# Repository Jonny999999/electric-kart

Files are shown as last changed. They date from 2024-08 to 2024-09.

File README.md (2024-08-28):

Firmware for Atmega-8 Microcontroller and kicad PCB-Files for a custom built electric kart.  
**Note:** The firmware and PCB files Version V1 were originally created in 2015, those have been added to this repository for archival purposes.

<br>

# Hardware Overview (vehicle)
- 2.9 kW Series wound motor (forklift)
- Custom pcb with Atmega-8 creating 124 Hz PWM
- Custom pcb with mosfet driver
- Custom pcb with relay on IGBT for emergency stop
- Audi gas pedal used as voltage divider 
- 600A IGBT (FUJI 1MBI600PX-140-01)
- Schottky diode

## Wiring plan
[doc/wiring-plan.drawio.pdf](doc/wiring-plan.drawio.pdf)
  
## Photos
<p align="center">
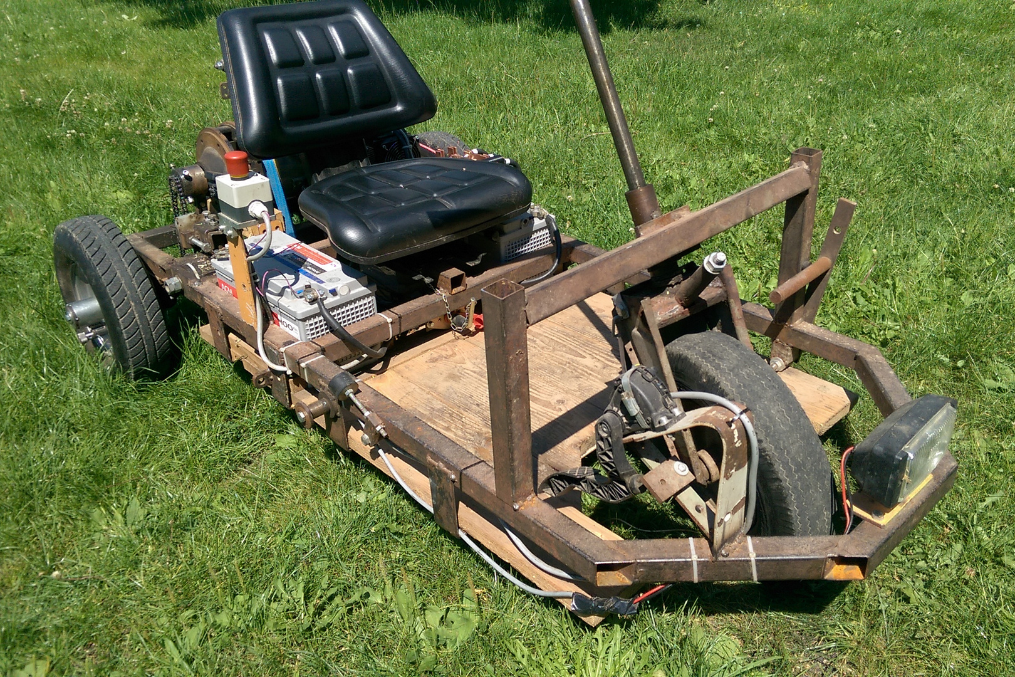
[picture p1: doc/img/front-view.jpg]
  
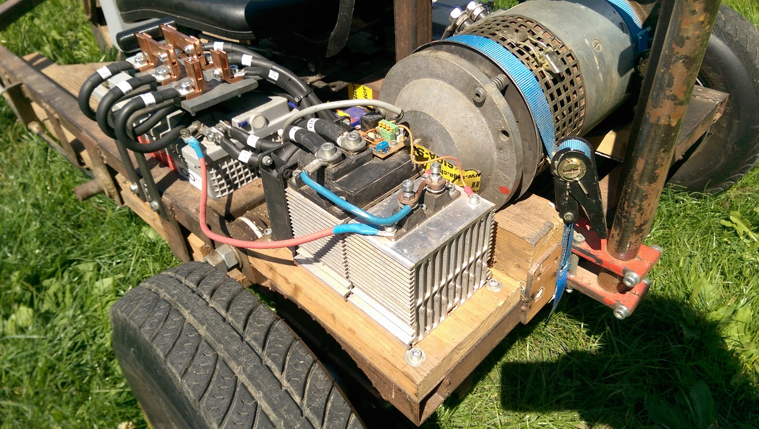
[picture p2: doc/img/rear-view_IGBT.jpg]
  
</p>

<br>

# Firmware
## Requirements
- avr-gcc
- avrdude
- make

## Compile
```bash
cd firmware/V1_fw-control-board
make
```

## Flash
Connect laptop to the board using an USB ISB-Programmer and run the commands:
```bash
make &&
sudo make upload
```
Note: `make upload` flashes the last compiled .elf file only  
-> also run `make` first for compiling and flashing the latest version.

## Current version
The current actually used project is located in [firmware/V2.1/](firmware/V2.1/).  
All other folders in [firmware/](firmware/) are for old board versions thus no longer used and archive only.

<br>

# Hardware (PCB Versions)
## V2.1
Rework of version V2.0 with more effort put into EMC to fix controller resets:
- 2 layer board
- 5V/GND for controller completely isolated from main batteries
  - isolated 5V DC-DC converter IC
  - more optocouplers: for driver, mosfet, relay and batt-voltage-threshold
- Strictly separate 5V and 24V components (separate GND planes, isolation gap)
- Front side is GND layer, Back side also has GND zones

Date: 2024.08.20  
Folder: [hardware/V2.1_board-ecar_isolated](hardware/V2.1_board-ecar_isolated/)  
Schematic: [hardware/V2.1_board-ecar_isolated/export/schematic.pdf](hardware/V2.1_board-ecar_isolated/export/schematic.pdf)
<br>
<br>
<p align="center">


</p>
<p align="center">

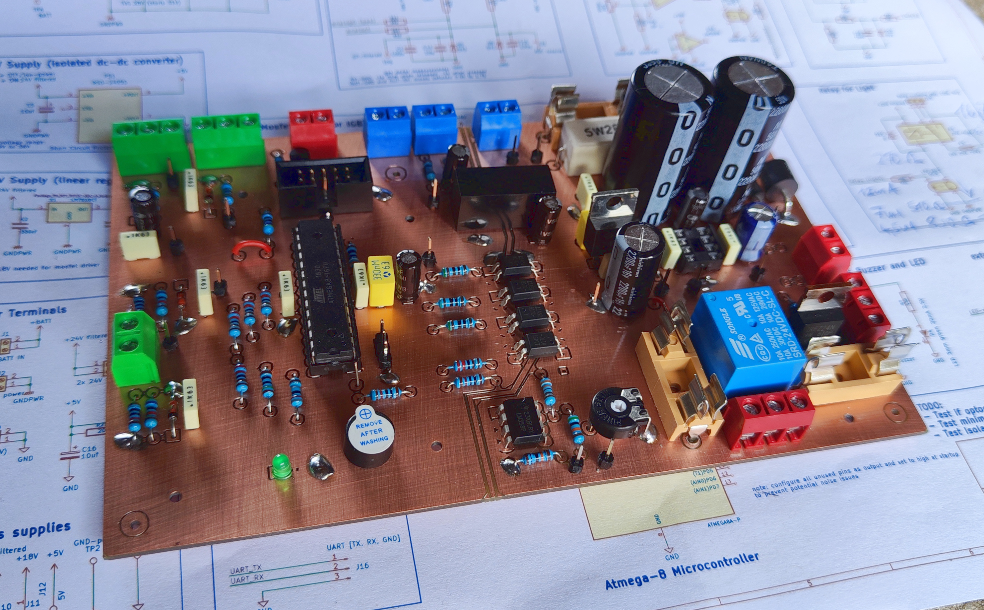
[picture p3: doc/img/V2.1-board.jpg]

</p>

## V2.0
V1.1 worked well for almost 9 years, the idea was to replace the corroded pcb and get rid of the separate supply batteries for the control board.  
Single board with controller, driver and newly added:
- supply filter
- buck converter
- relay  
  
Date: 2024.08.06  
Folder: [hardware/V2.0_board-ecar](hardware/V2.0_board-ecar)  
Schematic: [hardware/V2.0_board-ecar/export/schematic.pdf](hardware/V2.0_board-ecar/export/schematic.pdf)
<br>
<br>
<p align="center">

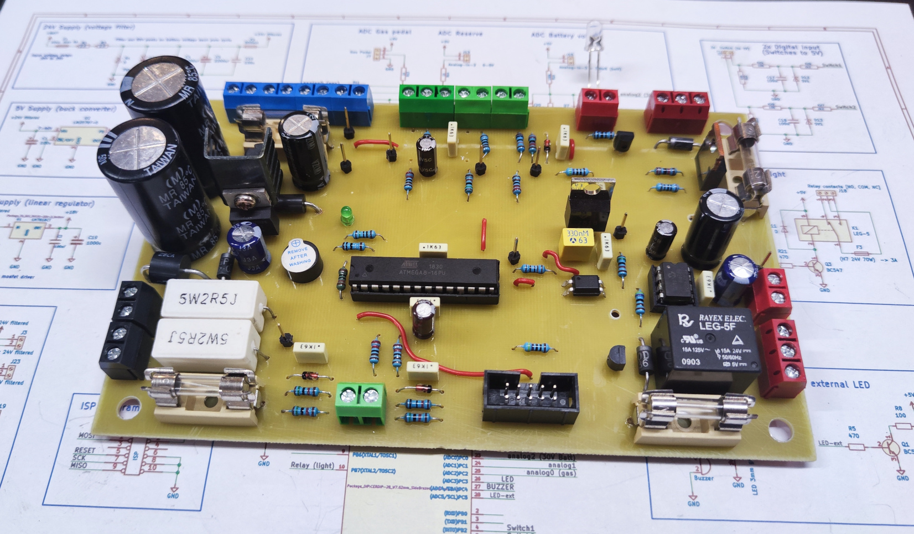
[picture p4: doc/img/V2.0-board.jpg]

</p>

**Fail:**  
Same problems as previous versions: When main batteries are used as supply for control pcb, the controller crashes at certain duty cycle.  
When Using an isolated supply (separate battery or lab supply) there is no issue. => peaks in supply voltage were not the issue and the filter did not really help, except preventing the voltage-regulators from burning out.  
<br>
**Issues:**  
- bad GND track (driver current shifts GND level for controller)
- bad routing overall (EMC)
- UART connector missing
- GND testpin missing

## V1.1
**separate driver board**  
Same control board from V1.0 but additional separate pcb with mosfet driver.  
Date: 2015.05.24  
Folder: [hardware/V1.1_driver-board-separate](hardware/V1.1_driver-board-separate)  
Schematic: [hardware/V1.1_driver-board-separate/export/schematic.pdf](hardware/V1.1_driver-board-separate/export/schematic.pdf)
<br>
<br>
<p align="center">
  
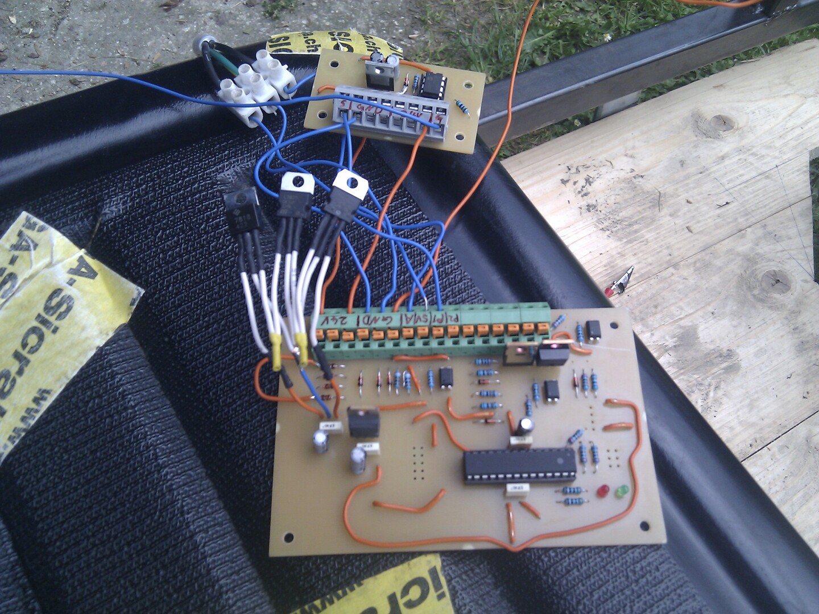
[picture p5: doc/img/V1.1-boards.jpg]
  
</p>

## V1.0
**control board**   
Date: 2015.05.14  
Folder: [hardware/V1.x_control-board](hardware/V1.x_control-board)  
Schematic: [hardware/V1.x_control-board/export/schematic.pdf](hardware/V1.x_control-board/export/schematic.pdf)
<br>
<br>


**Issues:**
- separate battery for control supply is necessary, when using main battery controller crashes when motor starts

**driver board on IGBT**  
pcb on IGBT with mosfet driver and relay (only the relay on this board is still used in V2.1)    
Folder: [hardware/V1.0_driver-board-on-igbt](hardware/V1.0_driver-board-on-igbt)  
Schematic: [hardware/V1.0_driver-board-on-igbt/export/schematic.pdf](hardware/V1.0_driver-board-on-igbt/export/schematic.pdf)
<br>
<br>
<p align="center">

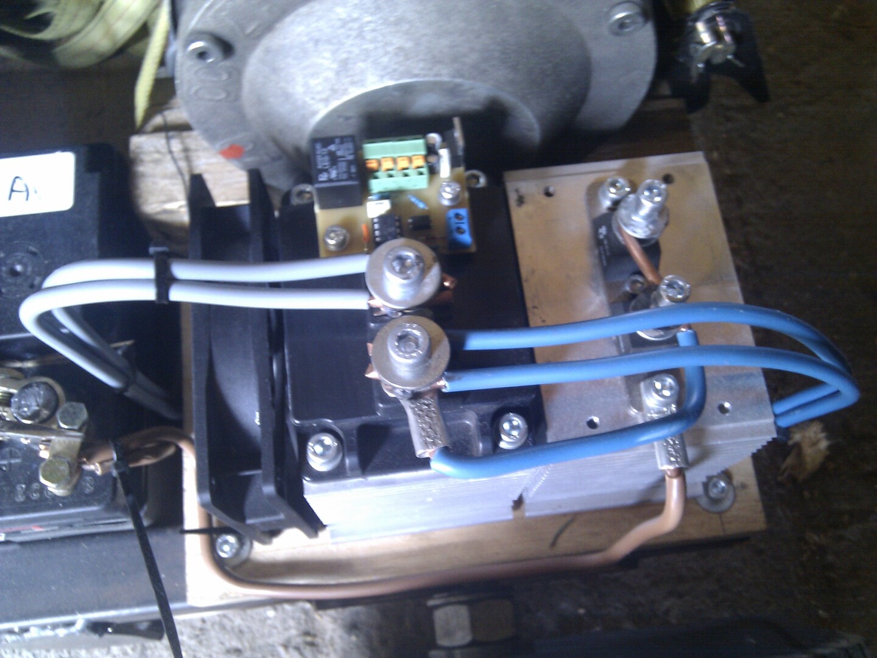
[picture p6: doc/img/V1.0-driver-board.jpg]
  
</p>

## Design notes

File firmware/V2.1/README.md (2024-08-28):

Firmware for control board version V2.1 (`hardware/V2.1_board-ecar_isolated`).  
This firmware project is started from scratch and is no longer based on the code from V1.  

# Usage
### Button
Pushbutton at the side of emergency stop switch:
- 1x short press: change configuration - rotates through config presets (different pwm frequencies and fan thresholds)
- 1x long press: toggle between normal and slow mode - in slow mode max duty is limited to certain percentage

### Switch
Toggle switch next to emergency stop switch:
- turn Relay on/off (light)

### Led
- blinks at startup
- always on when controller is running

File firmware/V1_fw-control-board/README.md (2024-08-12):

Firmware for control board version V1.x created in 2015

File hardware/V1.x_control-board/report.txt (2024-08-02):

Info: Backing up file '/home/jonny/projects/ecar/hardware_control/sym-lib-table' to '/home/jonny/projects/ecar/hardware_control/rescue-backup/sym-lib-table-2024-07-27-19-54-22'.
Info: Backing up file '/home/jonny/projects/ecar/hardware_control/control.sch' to '/home/jonny/projects/ecar/hardware_control/rescue-backup/control-2024-07-27-19-54-22.sch'.
Info: Backing up file '/home/jonny/projects/ecar/hardware_control/control.kicad_pro' to '/home/jonny/projects/ecar/hardware_control/rescue-backup/control-2024-07-27-19-54-22.kicad_pro'.
Info: Backing up file '/home/jonny/projects/ecar/hardware_control/control-cache.lib' to '/home/jonny/projects/ecar/hardware_control/rescue-backup/control-cache-2024-07-27-19-54-22.lib'.
Info: Backing up file '/home/jonny/projects/ecar/hardware_control/control-rescue.lib' to '/home/jonny/projects/ecar/hardware_control/rescue-backup/control-rescue-2024-07-27-19-54-22.lib'.
Info: Backing up file '/home/jonny/projects/ecar/hardware_control/control-rescue.dcm' to '/home/jonny/projects/ecar/hardware_control/rescue-backup/control-rescue-2024-07-27-19-54-22.dcm'.
Info: Adding library 'control-rescue', file '${KIPRJMOD}/control-rescue.lib' to project symbol library table.
Info: Adding library 'sfh620a', file '${KIPRJMOD}/lib/sfh620a.lib' to project symbol library table.
Info: Adding library '7805_correct_pins', file '${KIPRJMOD}/lib/7805_correct_pins.lib' to project symbol library table.
Symbol GND mapped to symbol library 'control-rescue'.
Symbol +12V mapped to symbol library 'control-rescue'.
Symbol DIODE mapped to symbol library 'control-rescue'.
Symbol +24V mapped to symbol library 'control-rescue'.
Symbol R mapped to symbol library 'control-rescue'.
Symbol R mapped to symbol library 'control-rescue'.
Symbol DIODE mapped to symbol library 'control-rescue'.
Symbol C mapped to symbol library 'control-rescue'.
Symbol DIODE mapped to symbol library 'control-rescue'.
Symbol DIODE mapped to symbol library 'control-rescue'.
Symbol DIODE mapped to symbol library 'control-rescue'.
Symbol +24V mapped to symbol library 'control-rescue'.
Symbol CONN_3X2 mapped to symbol library 'control-rescue'.
Symbol VCC mapped to symbol library 'control-rescue'.
Symbol VCC mapped to symbol library 'control-rescue'.
Symbol R mapped to symbol library 'control-rescue'.
Symbol GND mapped to symbol library 'control-rescue'.
Symbol VCC mapped to symbol library 'control-rescue'.
Symbol VCC mapped to symbol library 'control-rescue'.
Symbol C mapped to symbol library 'control-rescue'.
Symbol GND mapped to symbol library 'control-rescue'.
Symbol C mapped to symbol library 'control-rescue'.
Symbol GND mapped to symbol library 'control-rescue'.
Symbol C mapped to symbol library 'control-rescue'.
Symbol CONN_4 mapped to symbol library 'control-rescue'.
Symbol VCC mapped to symbol library 'control-rescue'.
Symbol CONN_2 mapped to symbol library 'control-rescue'.
Symbol +24V mapped to symbol library 'control-rescue'.
Symbol GND mapped to symbol library 'control-rescue'.
Symbol VCC mapped to symbol library 'control-rescue'.
Symbol GND mapped to symbol library 'control-rescue'.
Symbol GND mapped to symbol library 'control-rescue'.
Symbol CONN_5X2 mapped to symbol library 'control-rescue'.
Symbol VCC mapped to symbol library 'control-rescue'.
Symbol GND mapped to symbol library 'control-rescue'.
Symbol GND mapped to symbol library 'control-rescue'.
Symbol C mapped to symbol library 'control-rescue'.
Symbol GND mapped to symbol library 'control-rescue'.
Symbol +12V mapped to symbol library 'control-rescue'.
Symbol C mapped to symbol library 'control-rescue'.
Symbol GND mapped to symbol library 'control-rescue'.
Symbol 7805_correct_pins mapped to symbol library 'control-rescue'.
Symbol C mapped to symbol library 'control-rescue'.
Symbol GND mapped to symbol library 'control-rescue'.
Symbol GND mapped to symbol library 'control-rescue'.
Symbol 7805_correct_pins mapped to symbol library 'control-rescue'.
Symbol C mapped to symbol library 'control-rescue'.
Symbol DIODE mapped to symbol library 'control-rescue'.
Symbol R mapped to symbol library 'control-rescue'.
Symbol ATMEGA8A-P mapped to symbol library 'control-rescue'.
Symbol R mapped to symbol library 'control-rescue'.
Symbol VCC mapped to symbol library 'control-rescue'.
Symbol GND mapped to symbol library 'control-rescue'.
Symbol VCC mapped to symbol library 'control-rescue'.
Symbol VCC mapped to symbol library 'control-rescue'.
Symbol CONN_2 mapped to symbol library 'control-rescue'.
Symbol GND mapped to symbol library 'control-rescue'.
Symbol SFH620A mapped to symbol library 'sfh620a'.
Symbol GND mapped to symbol library 'control-rescue'.
Symbol R mapped to symbol library 'control-rescue'.
Symbol R mapped to symbol library 'control-rescue'.
Symbol R mapped to symbol library 'control-rescue'.
Symbol CONN_2 mapped to symbol library 'control-rescue'.
Symbol +24V mapped to symbol library 'control-rescue'.
Symbol LED mapped to symbol library 'control-rescue'.
Symbol GND mapped to symbol library 'control-rescue'.
Symbol GND mapped to symbol library 'control-rescue'.
Symbol SFH620A mapped to symbol library 'sfh620a'.
Symbol R mapped to symbol library 'control-rescue'.
Symbol LED mapped to symbol library 'control-rescue'.
Symbol R mapped to symbol library 'control-rescue'.
Symbol R mapped to symbol library 'control-rescue'.
Symbol R mapped to symbol library 'control-rescue'.
Symbol CONN_2 mapped to symbol library 'control-rescue'.
Symbol GND mapped to symbol library 'control-rescue'.
Symbol CONN_2 mapped to symbol library 'control-rescue'.
Symbol R mapped to symbol library 'control-rescue'.
Symbol CONN_2 mapped to symbol library 'control-rescue'.
Symbol R mapped to symbol library 'control-rescue'.
Symbol ZENER mapped to symbol library 'control-rescue'.
Symbol GND mapped to symbol library 'control-rescue'.
Symbol ZENER mapped to symbol library 'control-rescue'.
Symbol GND mapped to symbol library 'control-rescue'.
Symbol CONN_2 mapped to symbol library 'control-rescue'.
Symbol CONN_2 mapped to symbol library 'control-rescue'.
Symbol R mapped to symbol library 'control-rescue'.
Symbol CONN_3 mapped to symbol library 'control-rescue'.
Symbol CONN_3 mapped to symbol library 'control-rescue'.
Symbol GND mapped to symbol library 'control-rescue'.
Symbol R mapped to symbol library 'control-rescue'.
Symbol R mapped to symbol library 'control-rescue'.
Symbol ZENER mapped to symbol library 'control-rescue'.
Symbol GND mapped to symbol library 'control-rescue'.
Symbol GND mapped to symbol library 'control-rescue'.
Symbol ZENER mapped to symbol library 'control-rescue'.
Symbol ZENER mapped to symbol library 'control-rescue'.
Symbol R mapped to symbol library 'control-rescue'.
Symbol GND mapped to symbol library 'control-rescue'.
Symbol GND mapped to symbol library 'control-rescue'.
Symbol GND mapped to symbol library 'control-rescue'.
Symbol SFH620A mapped to symbol library 'sfh620a'.
Symbol GND mapped to symbol library 'control-rescue'.
Symbol R mapped to symbol library 'control-rescue'.
Symbol VCC mapped to symbol library 'control-rescue'.
Symbol R mapped to symbol library 'control-rescue'.
Info: Symbol library table mapping complete!
Info: Created project symbol library table.

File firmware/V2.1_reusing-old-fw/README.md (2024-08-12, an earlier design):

Firmware for control board version V2.0 while mostly reusing the code from V1.  
  
Additions:
- buzzer at startup
- turn on relay with switch (light)

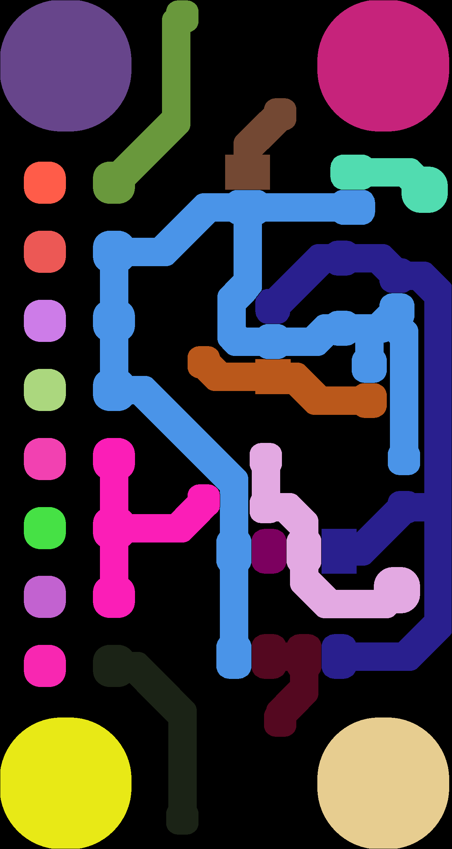
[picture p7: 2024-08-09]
hardware/V1.1_driver-board-separate/gcode-treiber/outp1_traced.png

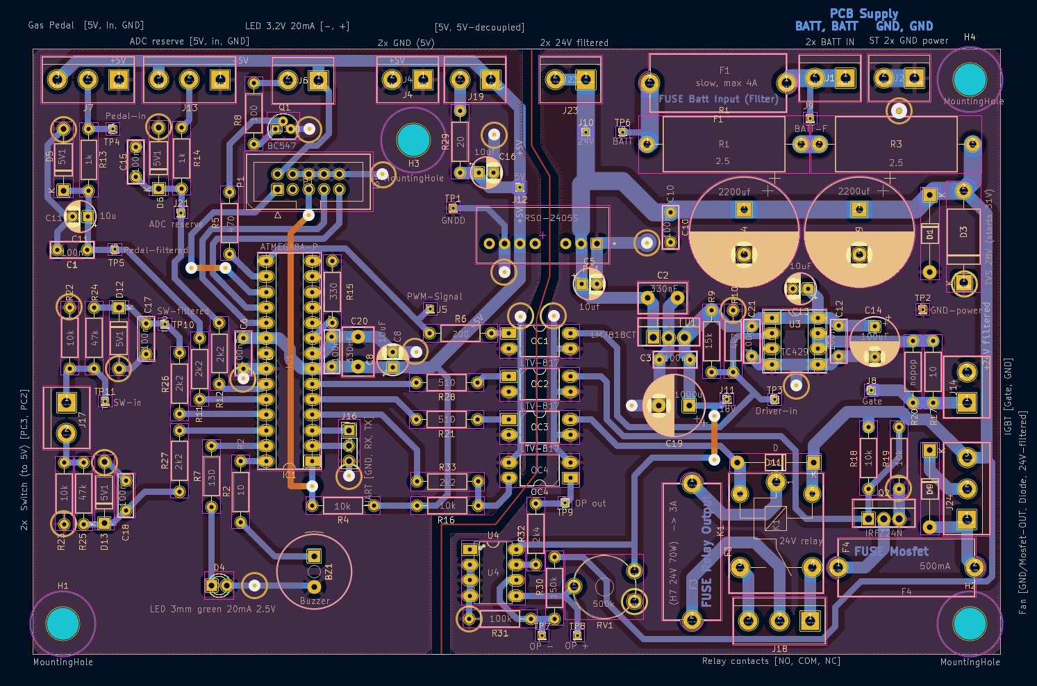
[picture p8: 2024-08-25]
hardware/V2.1_board-ecar_isolated/export/layout-with-zones.jpg

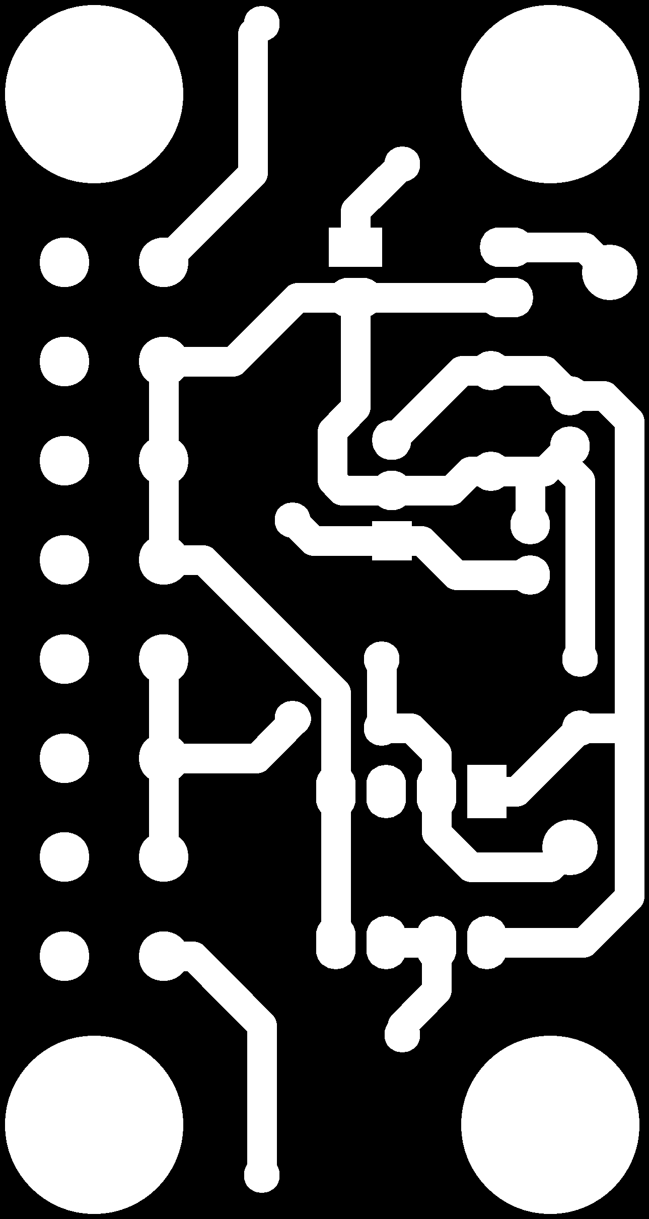
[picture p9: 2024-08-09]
hardware/V1.1_driver-board-separate/gcode-treiber/outp0_original_back.png

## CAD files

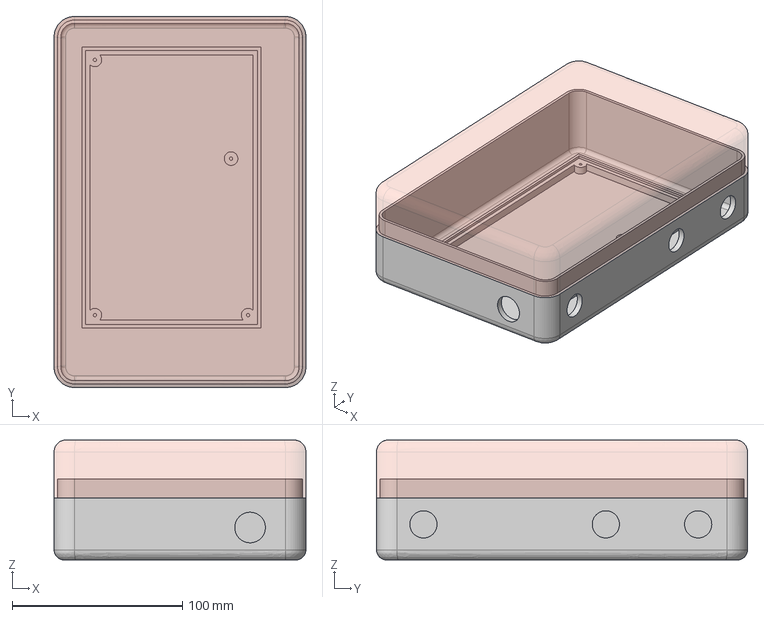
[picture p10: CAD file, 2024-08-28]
cad/box-control-board/box-control.FCStd
148.0 x 218.0 x 70.5 mm
bot
lid

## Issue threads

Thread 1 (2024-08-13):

PWM signal not continous

Jonny999999, 2024-08-13:
# issue
There are gaps in the pwm signal, especially at low duty cycle (gas pedal less than 5% pressed)
Noticed the clicking in sound since 2015, but it did not really bother me much...
Just saw it on scope while debugging:
# screenshots
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
(pressing gas pedal 5-10%)

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
pressing gas pedal 2%, you can hear the gaps clicking in the motor

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
pressing ~20%

Jonny999999, 2024-09-02:
Did not notice that issue anymore in newly created and currently used firmware/V2.1/

Closed 2024-09-02.

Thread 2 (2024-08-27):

Notes hardware

Jonny999999, 2024-08-27:
# Notes Board V2.1

## issues
- temperaturesensor for igbt missing
- Mosfet output does not switch off / on completely

## Tasks
-[ ] reduce gate resistor after driver <10 ohm for less switching losses
-[ ] 18V 1.5A supply powerfull enough?
-[ ] replace mosfet / change resistors

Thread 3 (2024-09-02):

Dynamic PWM frequency

Jonny999999, 2024-09-02:
- high frequencies at low duty / start
- low frequencies at high duty / driving

# idea
-> less noise when starting,  less switching losses at high speed

low frequencies at about 40% causes very loud vibrations  -> change to higher frequency in that range

# tasks
needs testing to find out good frequencies and duty thresholds

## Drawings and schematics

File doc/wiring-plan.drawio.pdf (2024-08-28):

UI:
switch (24V Supply),

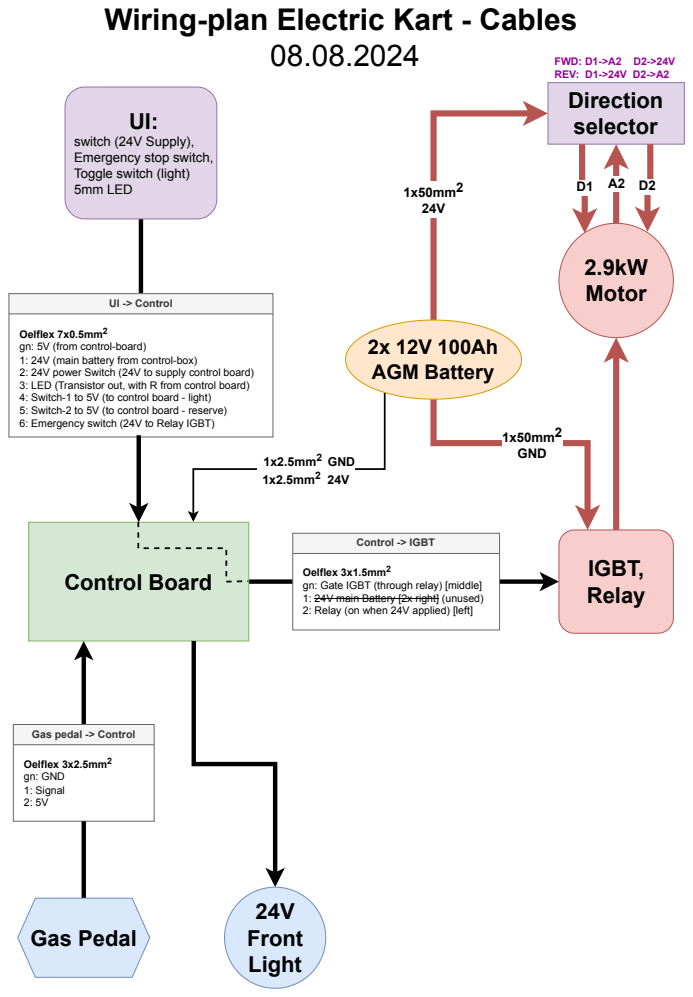
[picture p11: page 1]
Control Board; IGBT,; Relay; Control -> IGBT; Oelflex 3x2.5mm² gn: GND 1: Signal 2: 5V; Gas Pedal; 24V Front Light; UI -> Control; 1x2.5mm² GND 1x2.5mm²; 1x50mm2 GND; 2x 12V 100Ah AGM Battery; 2.9kW Motor; Direction selector; FWD: D1->A2 D2->24V REV: D1->24V D2->A2

Wiring-plan Electric Kart - Cables

Emergency stop switch,
Toggle switch (light)
5mm LED

Oelflex 7x0.5mm²
gn: 5V (from control-board)
1: 24V (main battery from control-box)
2: 24V power Switch (24V to supply control board)
3: LED (Transistor out, with R from control board)
4: Switch-1 to 5V (to control board - light)
5: Switch-2 to 5V (to control board - reserve)
6: Emergency switch (24V to Relay IGBT)

Oelflex 3x1.5mm²
gn: Gate IGBT (through relay) [middle]
1: 24V main Battery [2x right] (unused)
2: Relay (on when 24V applied) [left]

Gas pedal -> Control

# Wiring-plan Electric Kart - Motor

27.08.2024

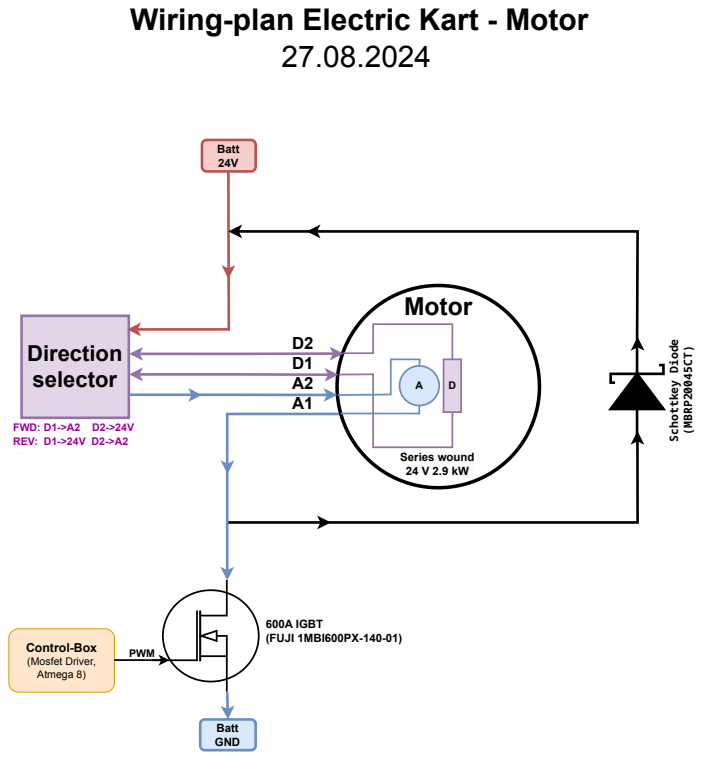
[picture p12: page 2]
FWD: D1->A2 D2->24V REV: D1->24V D2->A2; Motor; Direction selector; Series wound 24 V 2.9 kW; Batt 24V; Batt GND; 600A IGBT (FUJI 1MBI600PX-140-01); Schottkey; Diode (MBRP20045CT); Control-Box (Mosfet Driver, Atmega 8); PWM

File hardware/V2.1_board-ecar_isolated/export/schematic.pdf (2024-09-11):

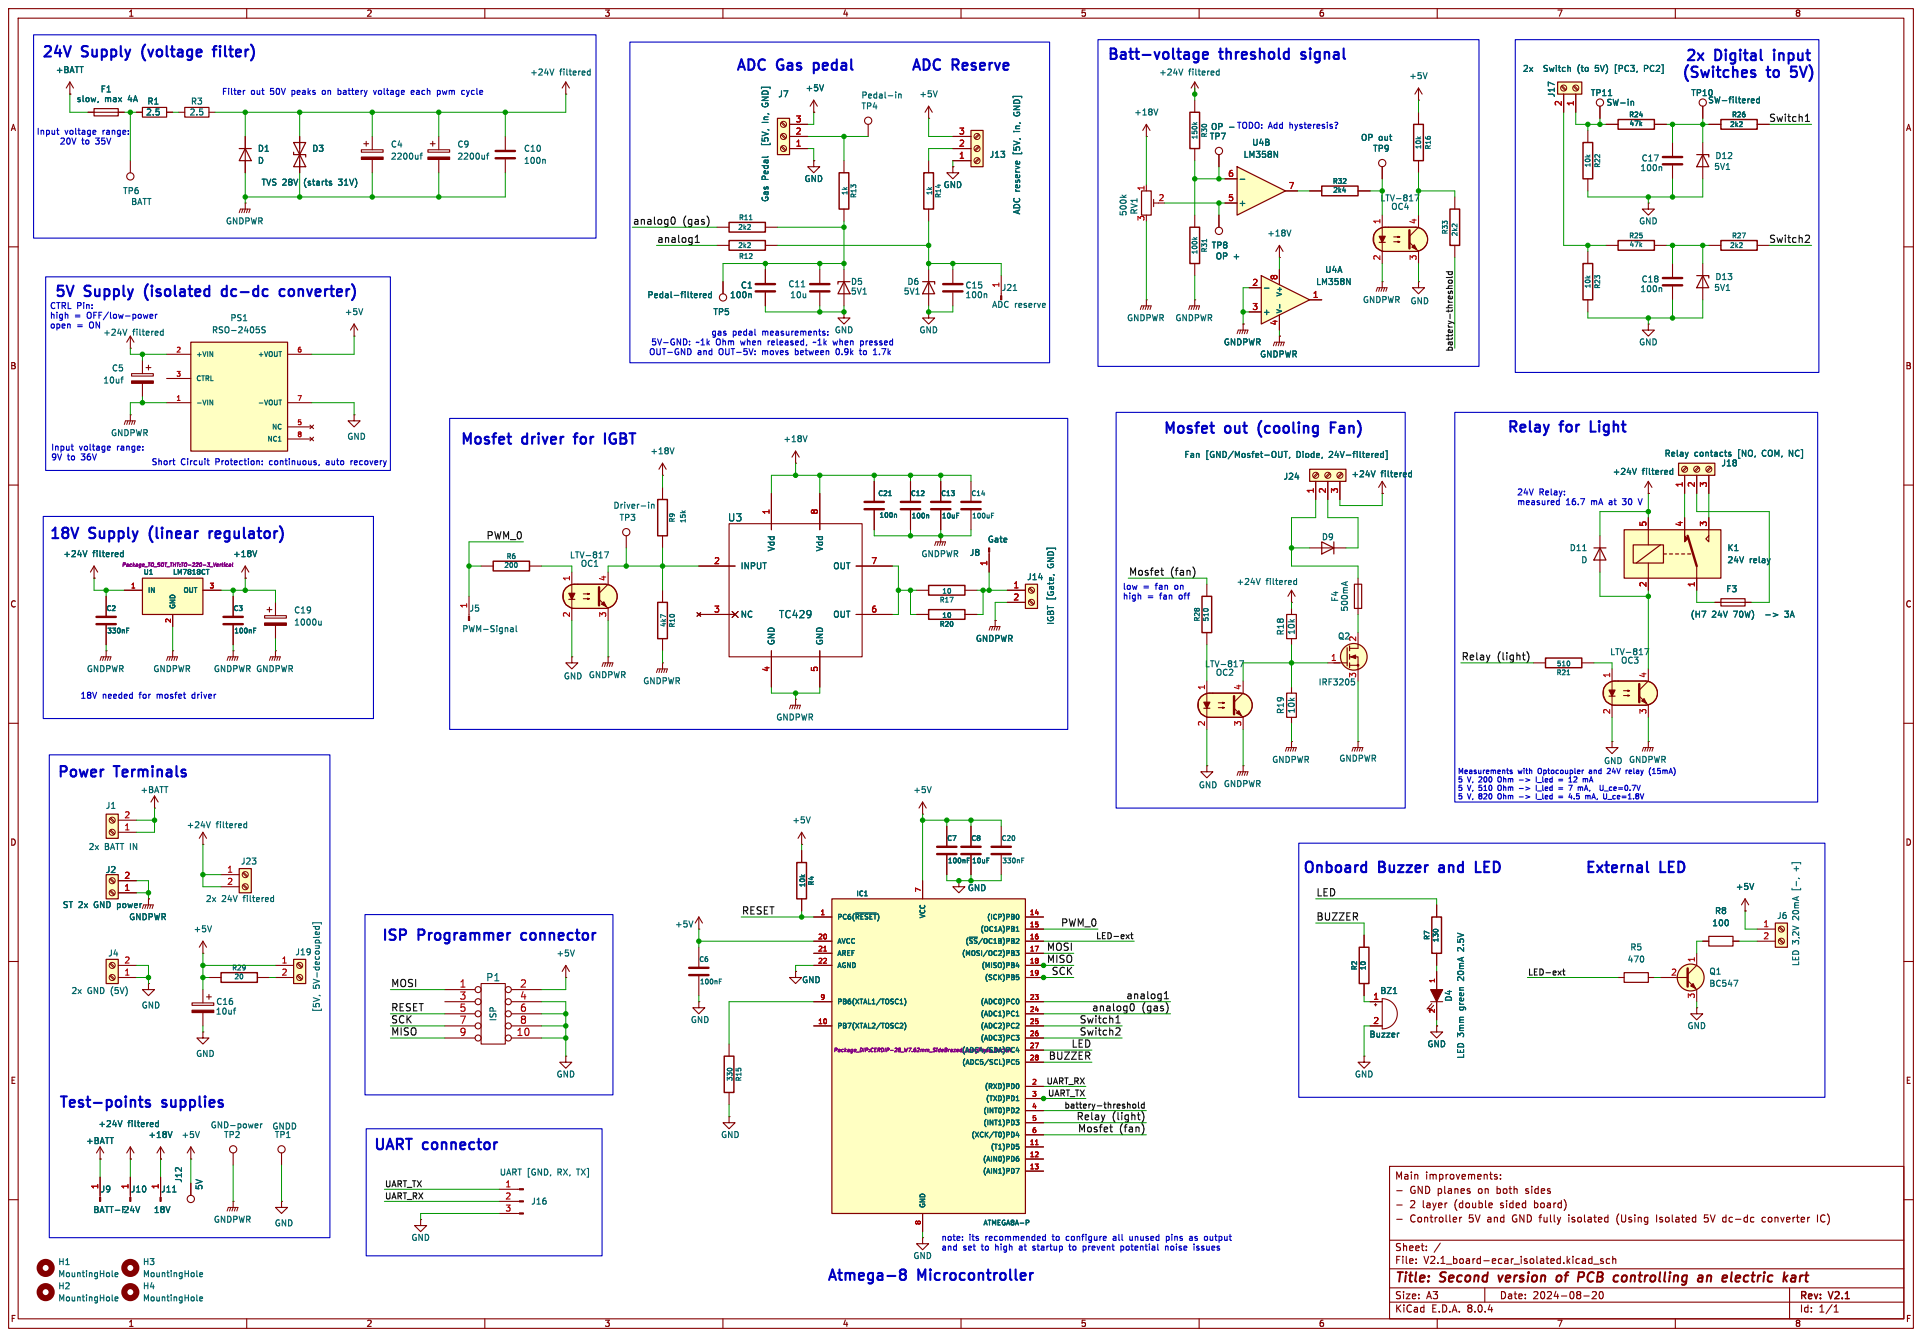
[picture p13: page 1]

J13 ADC reserve [5V, in, GND] +5V +5V GND

J13 ADC reserve [5V, in, GND] 1

Mosfet driver for IGBT

high = fan off Power Terminals

LED-ext Relay (light)

Onboard Buzzer and LED

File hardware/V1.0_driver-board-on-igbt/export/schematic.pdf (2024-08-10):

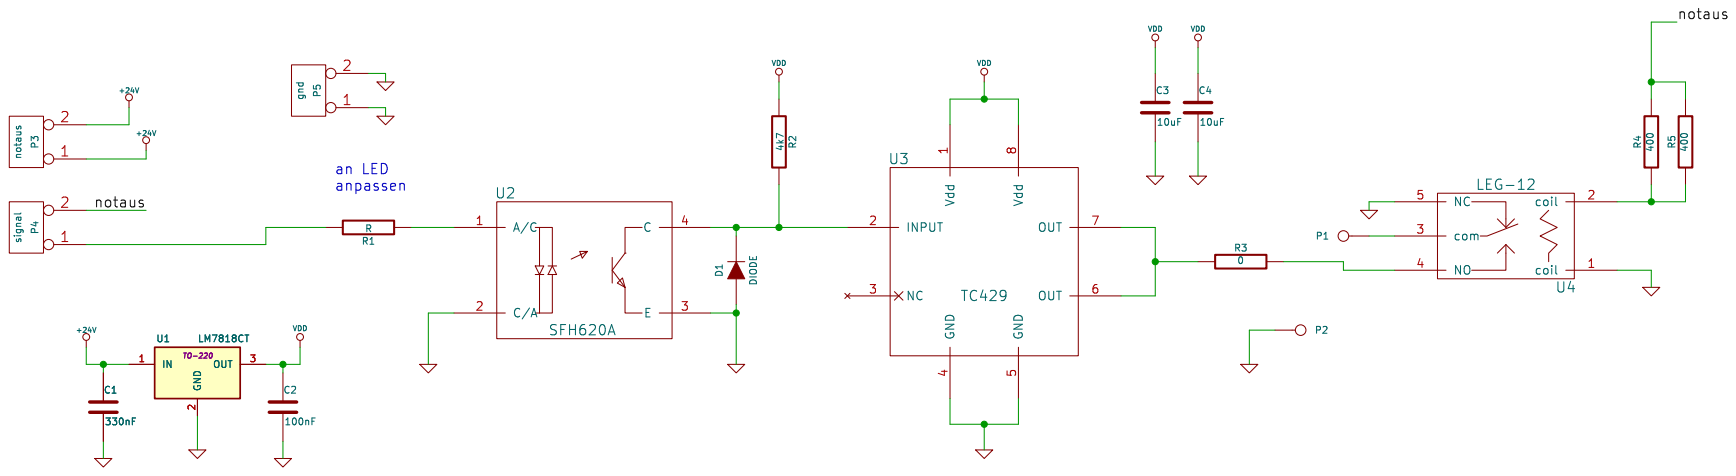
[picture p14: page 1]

Id: 1/1 Title: File: treiber.kicad_sch Sheet: /

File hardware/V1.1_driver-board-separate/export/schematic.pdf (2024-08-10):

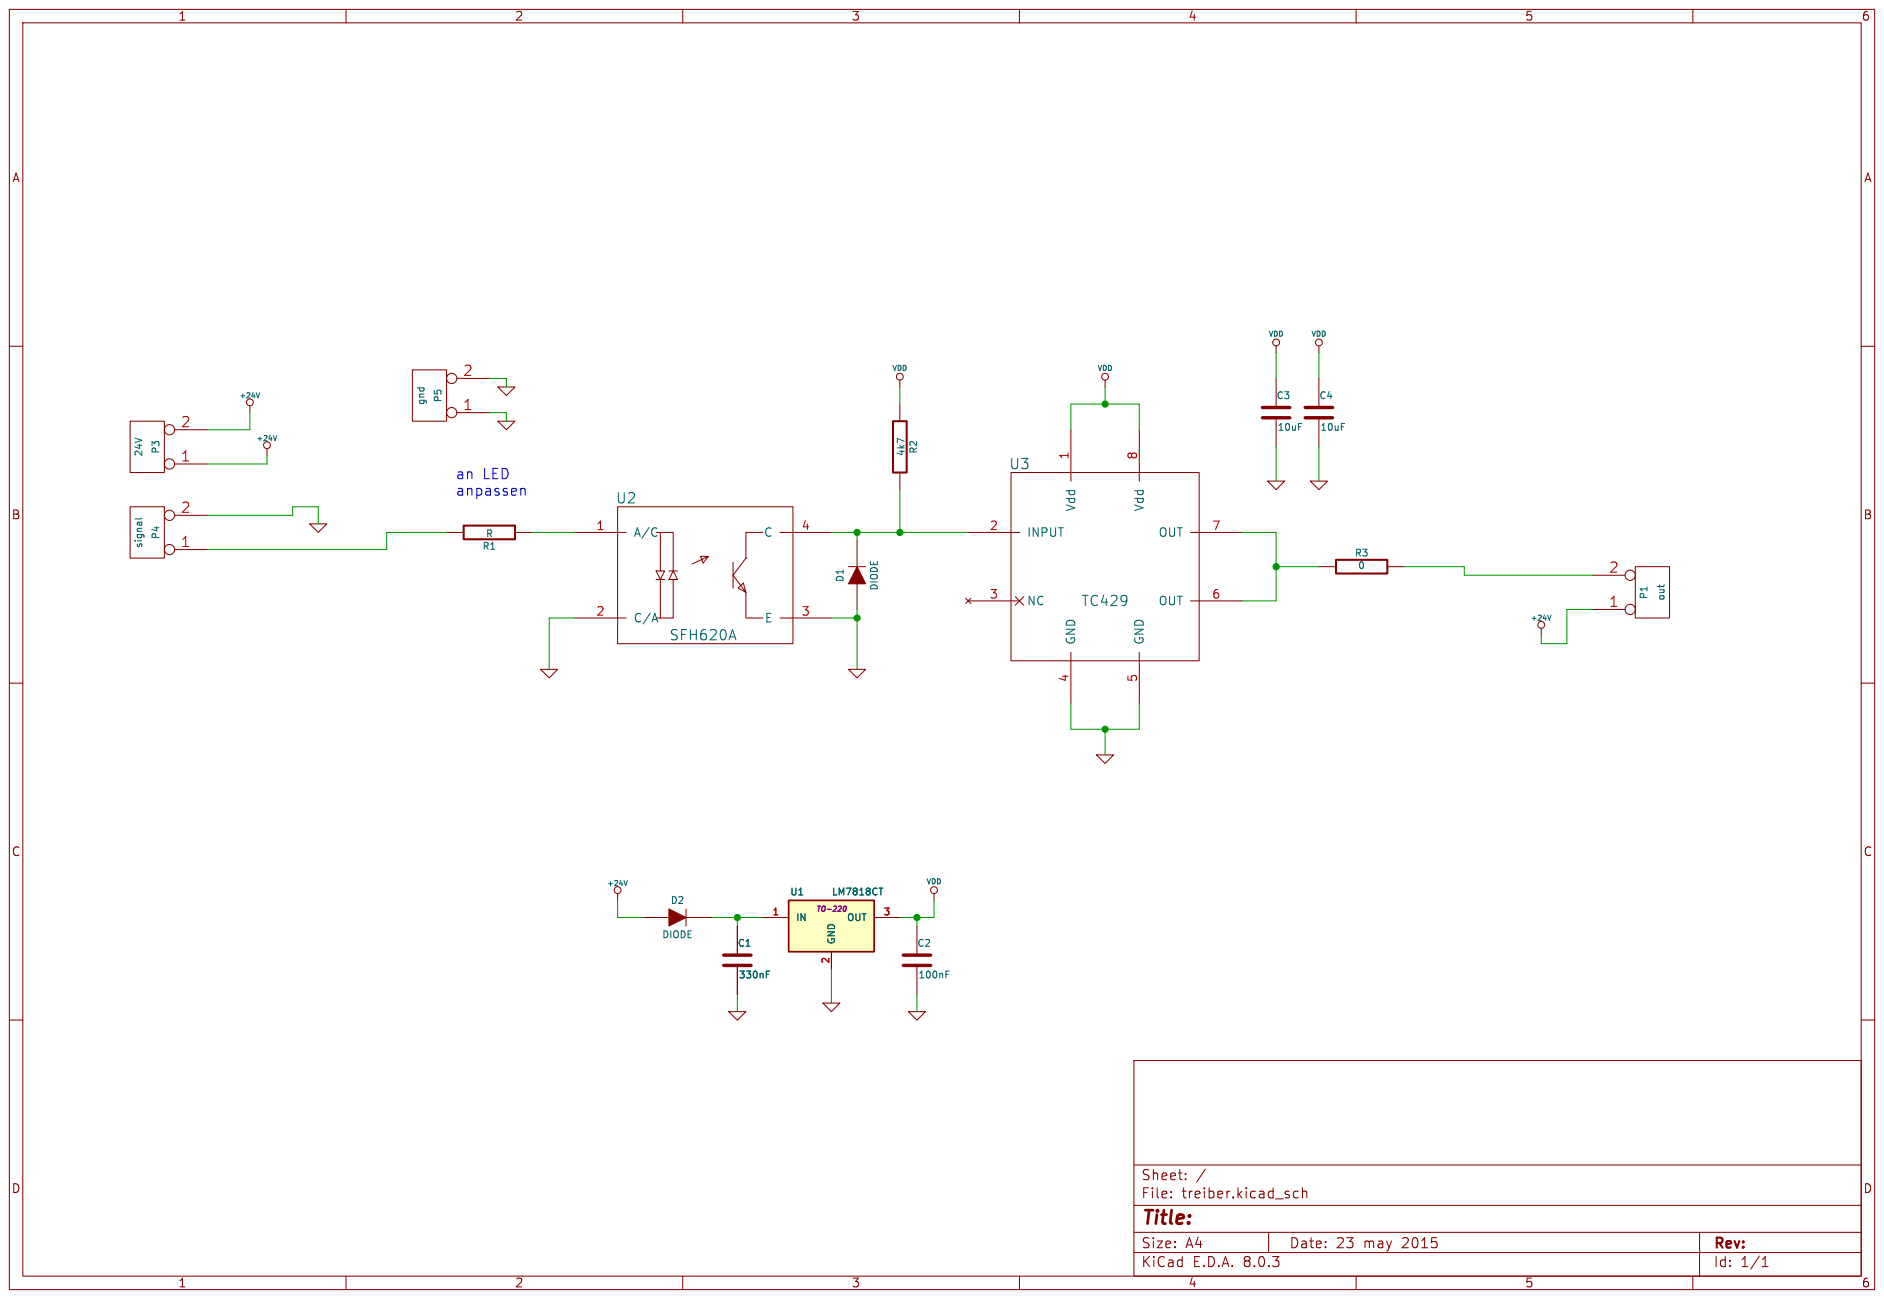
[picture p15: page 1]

Id: 1/1 Title: File: treiber.kicad_sch Sheet: /

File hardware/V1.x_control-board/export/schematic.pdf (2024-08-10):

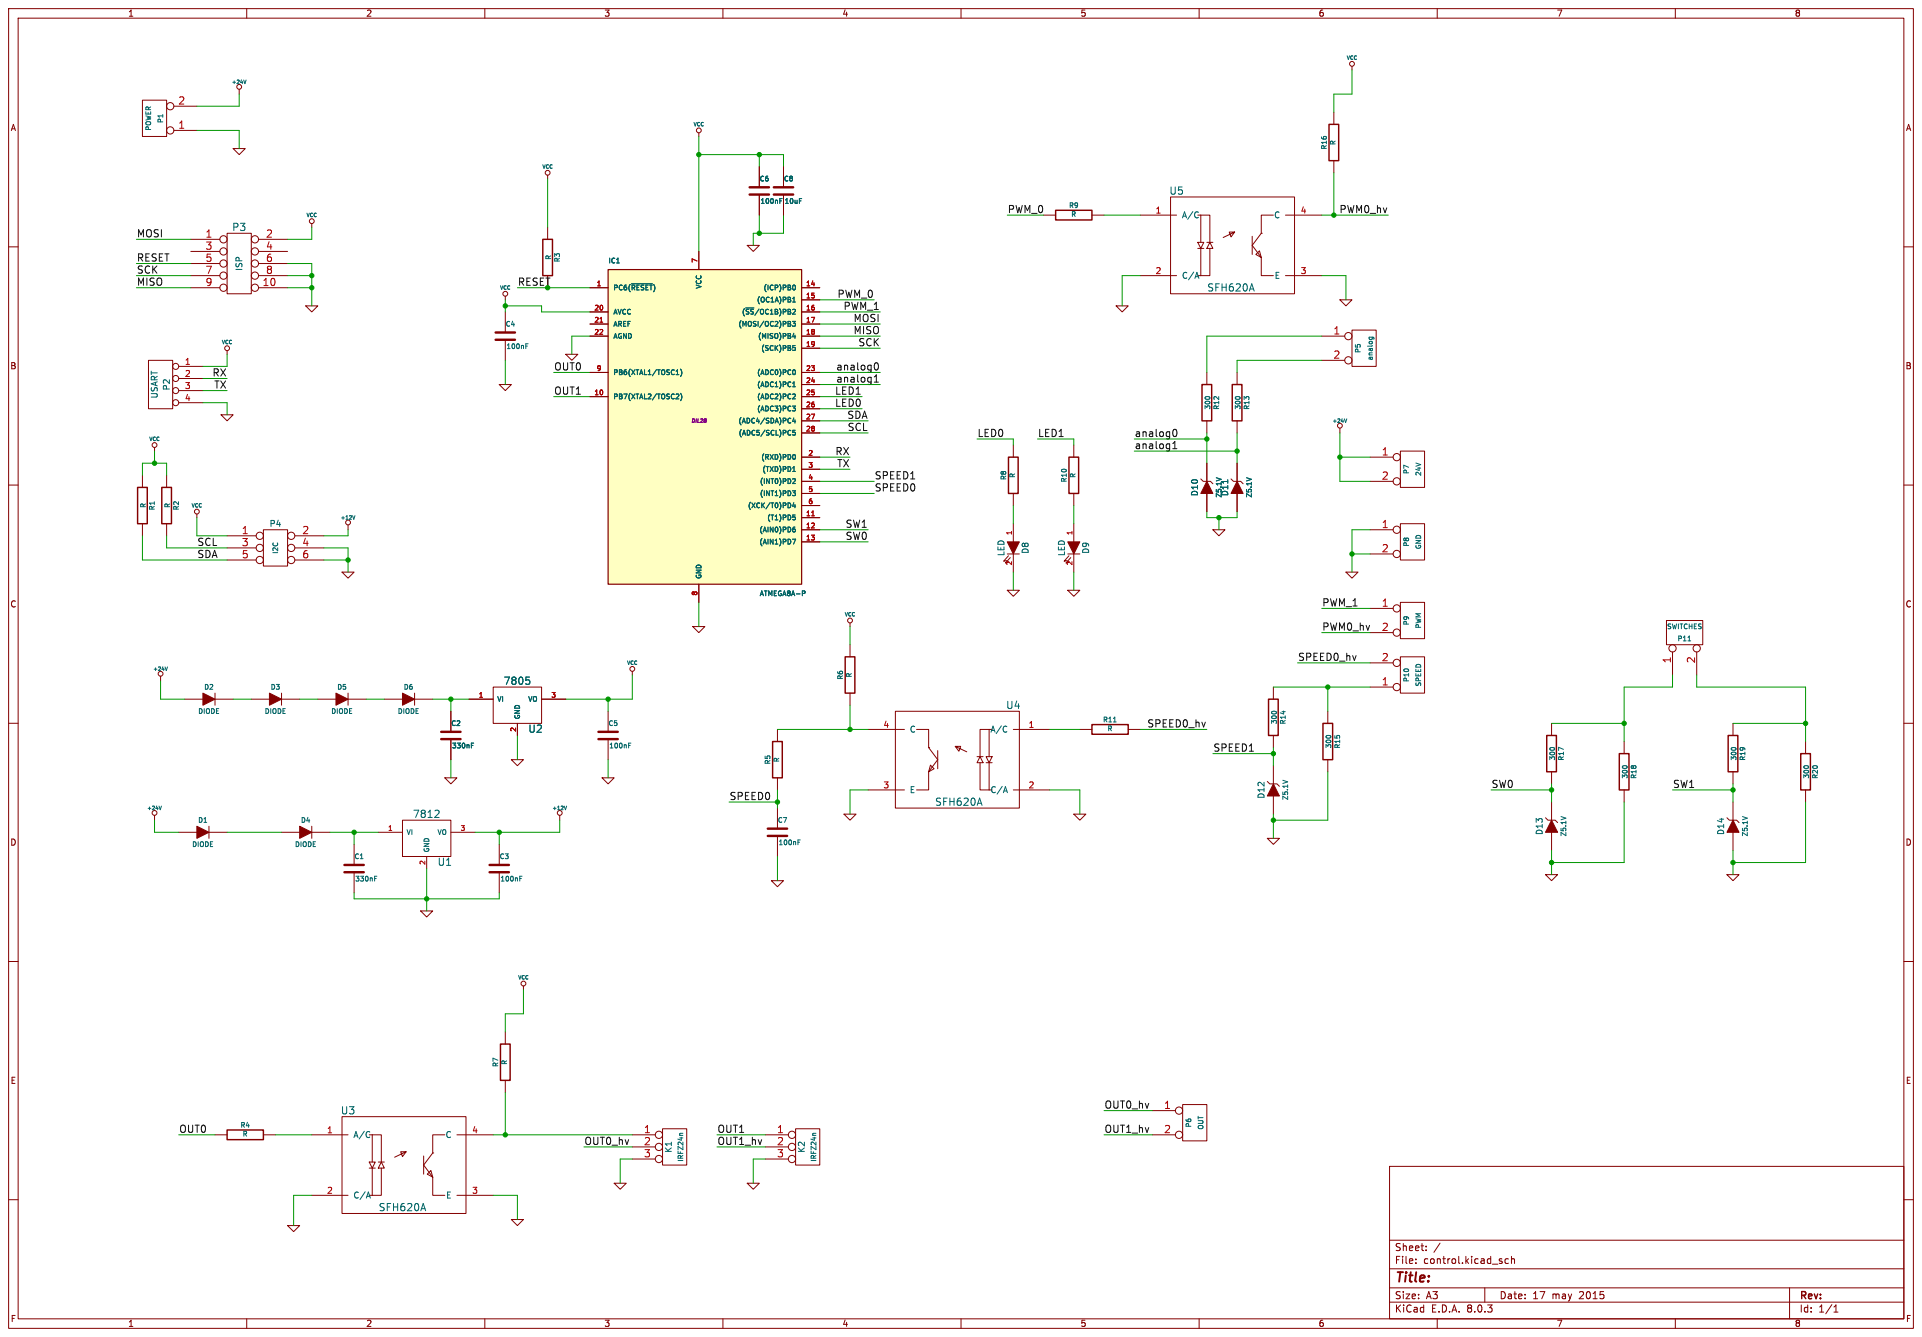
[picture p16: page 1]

Id: 1/1 Title: File: control.kicad_sch Sheet: / R10R

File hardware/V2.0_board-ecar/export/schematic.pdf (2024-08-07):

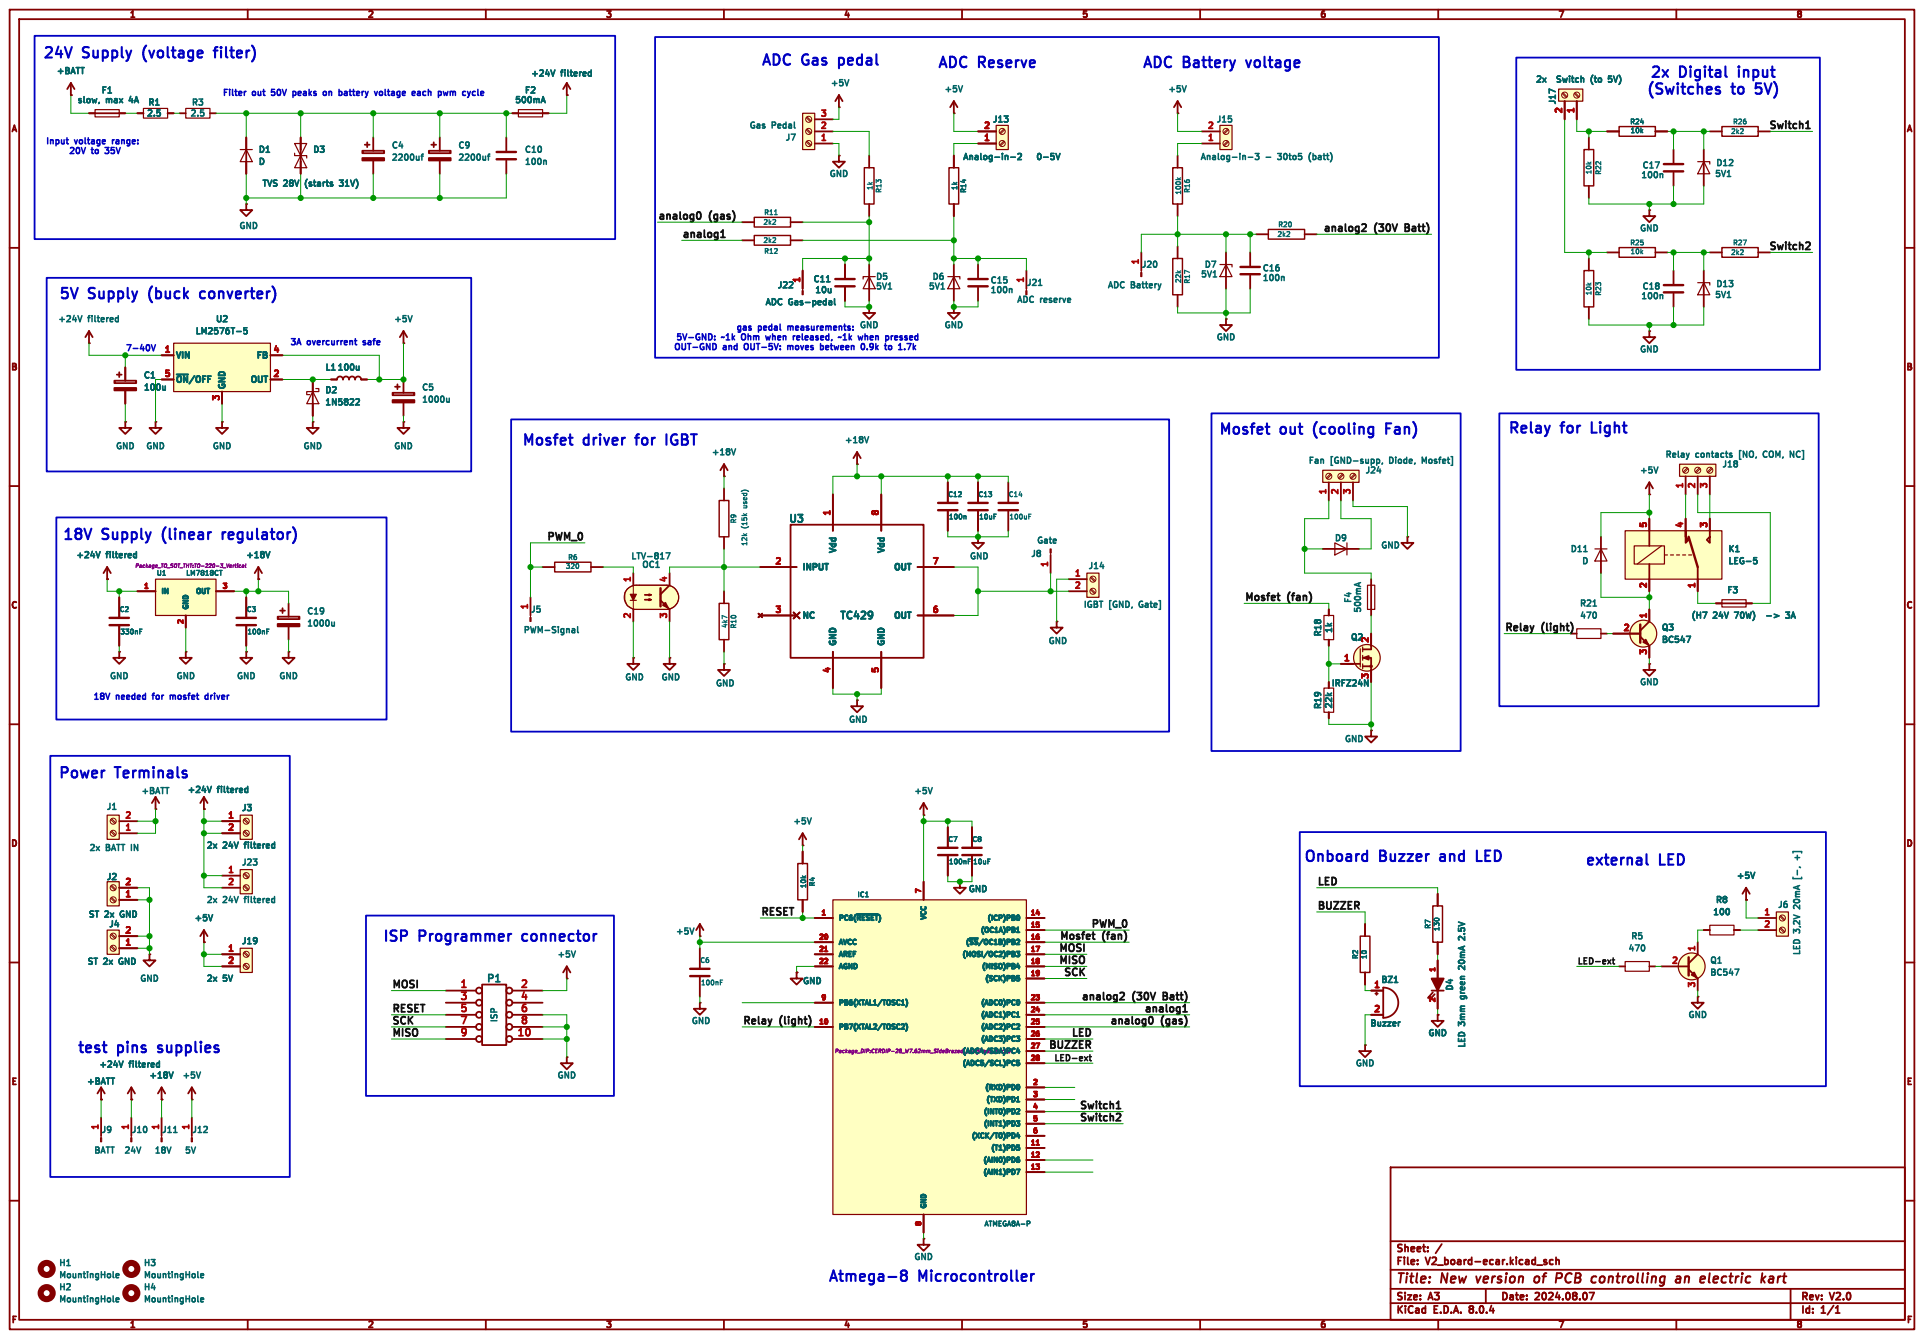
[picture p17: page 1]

Mosfet out (cooling Fan)

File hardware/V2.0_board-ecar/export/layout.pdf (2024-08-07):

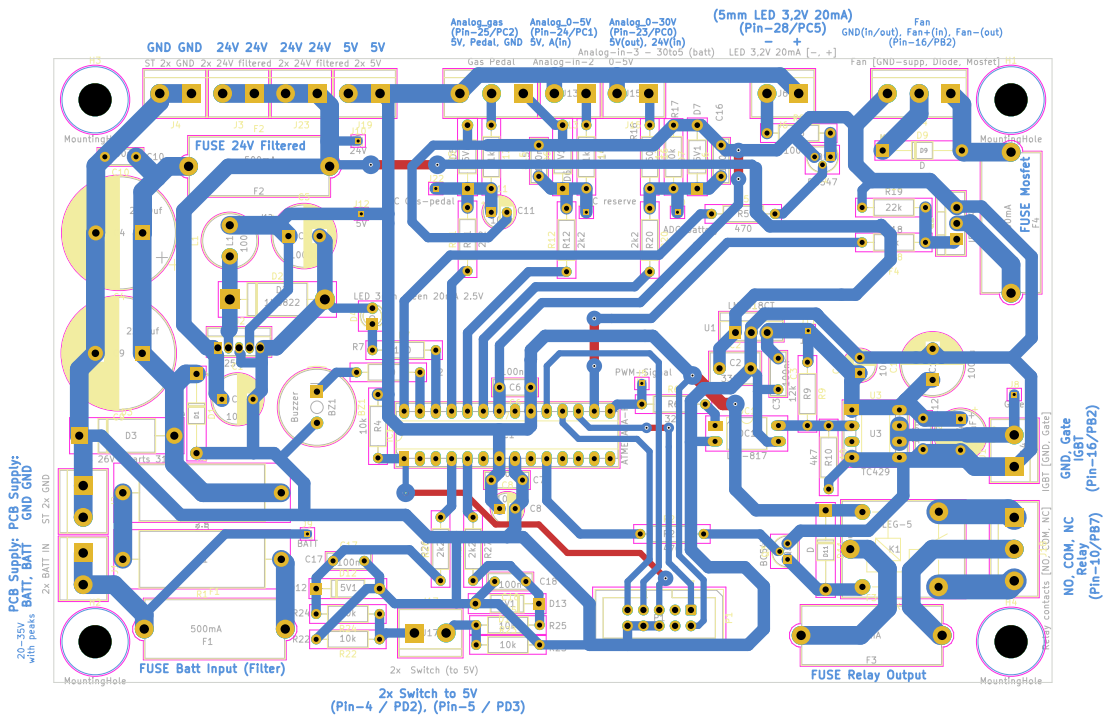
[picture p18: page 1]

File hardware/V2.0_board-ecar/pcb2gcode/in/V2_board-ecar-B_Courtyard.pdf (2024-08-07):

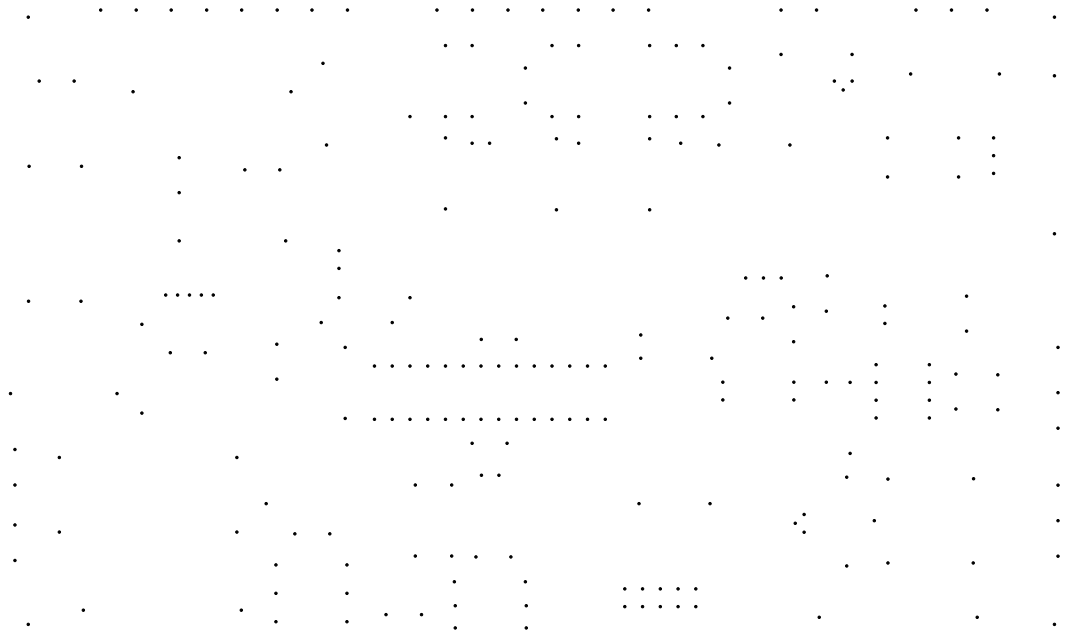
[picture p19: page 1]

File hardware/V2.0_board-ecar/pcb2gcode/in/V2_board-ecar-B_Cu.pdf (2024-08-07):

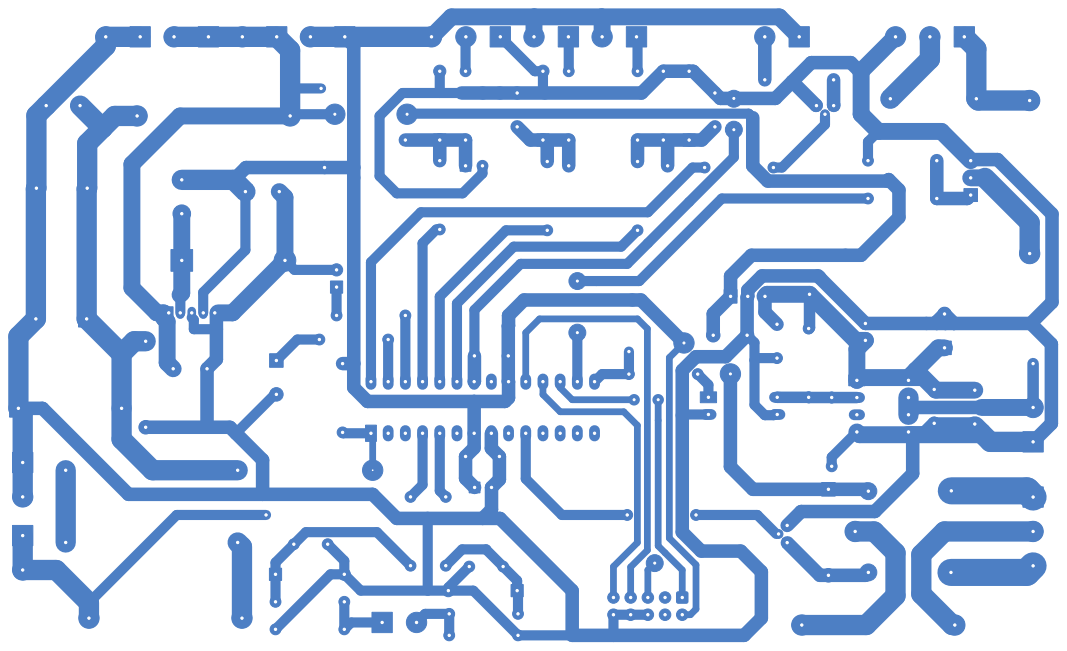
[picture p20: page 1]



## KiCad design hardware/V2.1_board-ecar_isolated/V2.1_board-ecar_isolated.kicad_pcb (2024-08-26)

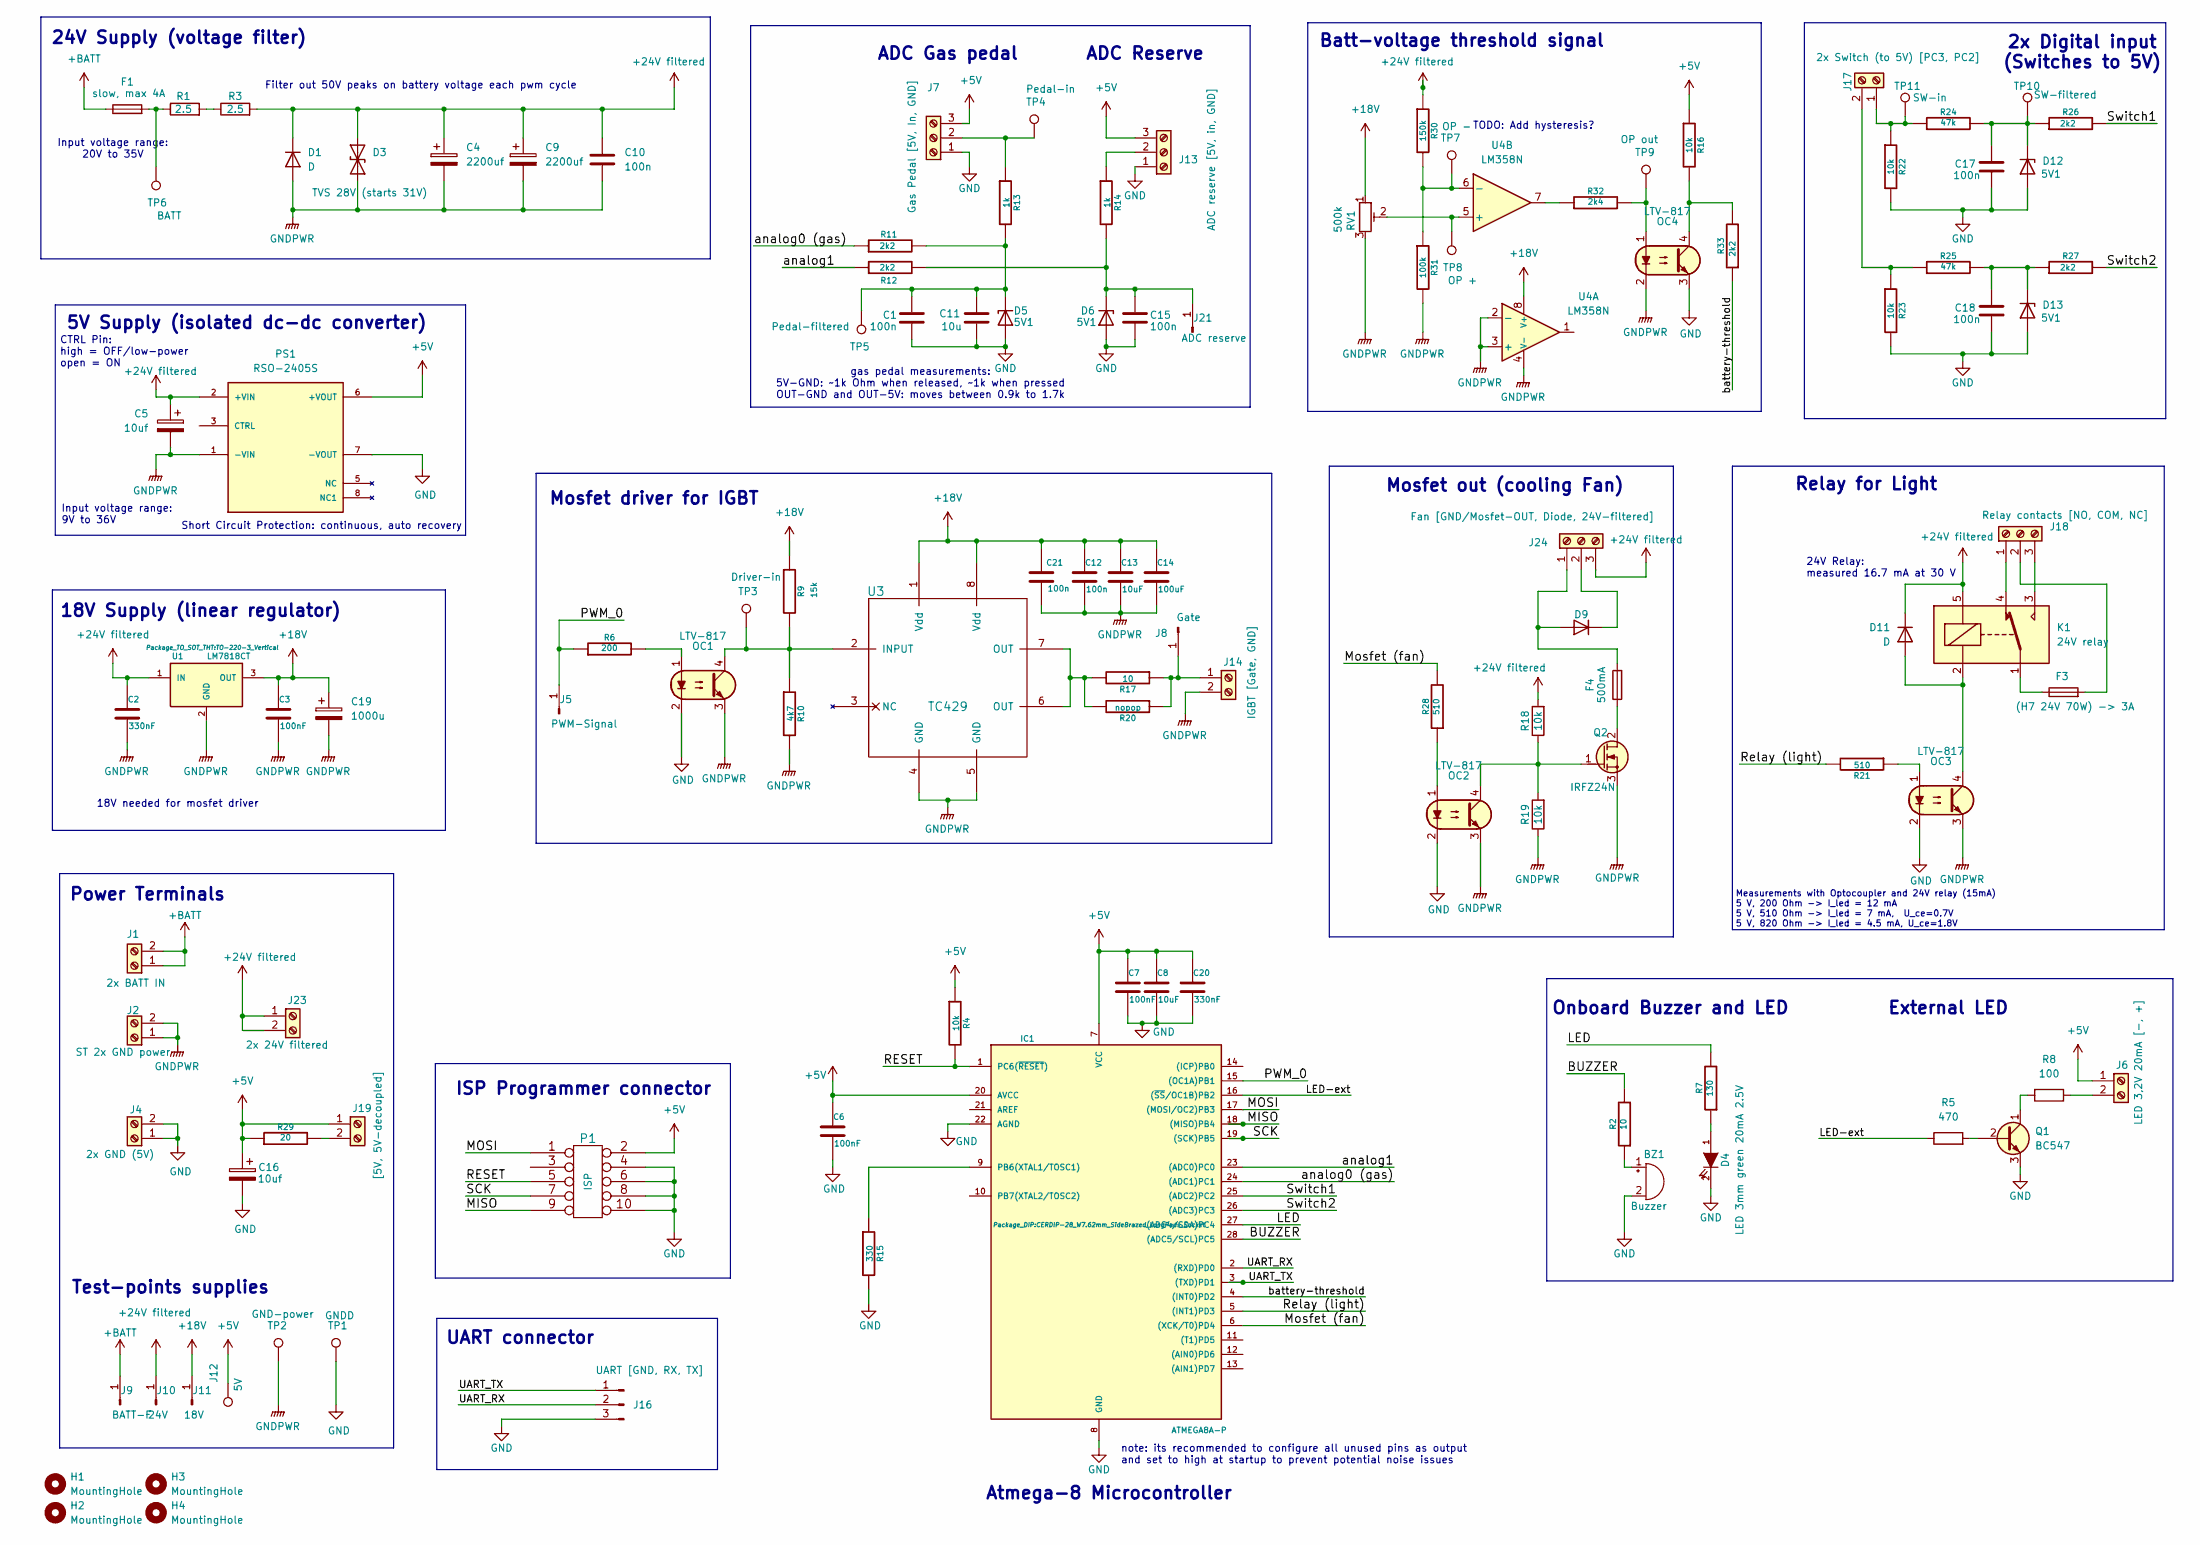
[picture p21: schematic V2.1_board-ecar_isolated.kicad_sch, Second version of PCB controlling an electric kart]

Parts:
BZ1: Buzzer; Buzzer_TDK_PS1240P02BT_D12.2mm_H6.5mm
C1, C10, C12, C15, C17, C18, C21: 100n; C_Disc_D7.0mm_W2.5mm_P5.00mm
C2, C20: 330nF; C_Disc_D8.0mm_W5.0mm_P5.00mm
C3, C6, C7: 100nF; C_Disc_D7.0mm_W2.5mm_P5.00mm
C4, C9: 2200uf; CP_Radial_D18.0mm_P7.50mm
C5, C16: 10uf; CP_Radial_D5.0mm_P2.50mm
C8, C13: 10uF; CP_Radial_D5.0mm_P2.50mm
C11: 10u; CP_Radial_D5.0mm_P2.50mm
C14: 100uF; CP_Radial_D8.0mm_P5.00mm
C19: 1000u; CP_Radial_D10.0mm_P5.00mm
D1, D9, D11: D; D_T-1_P12.70mm_Horizontal
D3: TVS 28V (starts 31V); D_DO-201AE_P15.24mm_Horizontal
D4: LED 3mm green 20mA 2.5V; LED_D3.0mm_Clear
D5, D6, D12, D13: 5V1; D_A-405_P10.16mm_Horizontal
F1: slow, max 4A; Fuseholder_Cylinder-5x20mm_Stelvio-Kontek_PTF78_Horizontal_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
F3: (H7 24V 70W) -> 3A; Fuseholder_Cylinder-5x20mm_Stelvio-Kontek_PTF78_Horizontal_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
F4: 500mA; Fuseholder_Cylinder-5x20mm_Stelvio-Kontek_PTF78_Horizontal_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
H1, H2, H3, H4: MountingHole; MountingHole_5.3mm_M5
IC1: ATMEGA8A-P; CERDIP-28_W7.62mm_SideBrazed_LongPads_Socket
J1: 2x BATT IN; TerminalBlock_bornier-2_P5.08mm
J2: ST 2x GND power; TerminalBlock_bornier-2_P5.08mm
J4: 2x GND (5V); TerminalBlock_bornier-2_P5.08mm
J5: PWM-Signal; PinHeader_1x01_P1.00mm_Vertical
J6: LED 3,2V 20mA [-, +]; TerminalBlock_bornier-2_P5.08mm
J7: Gas Pedal [5V, In, GND]; TerminalBlock_bornier-3_P5.08mm
J8: Gate; PinHeader_1x01_P1.00mm_Vertical
J9: BATT-F; PinHeader_1x01_P1.00mm_Vertical
J10: 24V; PinHeader_1x01_P1.00mm_Vertical
J11: 18V; PinHeader_1x01_P1.00mm_Vertical
J12: 5V; PinHeader_1x01_P1.00mm_Vertical
J13: ADC reserve [5V, in, GND]; TerminalBlock_bornier-3_P5.08mm
J14: IGBT [Gate, GND]; TerminalBlock_bornier-2_P5.08mm
J16: UART [GND, RX, TX]; PinHeader_1x03_P2.54mm_Vertical
J17: 2x Switch (to 5V) [PC3, PC2]; TerminalBlock_bornier-2_P5.08mm
J18: Relay contacts [NO, COM, NC]; TerminalBlock_bornier-3_P5.08mm
J19: [5V, 5V-decoupled]; TerminalBlock_bornier-2_P5.08mm
J21: ADC reserve; PinHeader_1x01_P1.00mm_Vertical
J23: 2x 24V filtered; TerminalBlock_bornier-2_P5.08mm
J24: Fan [GND/Mosfet-OUT, Diode, 24V-filtered]; TerminalBlock_bornier-3_P5.08mm
K1: 24V relay; Relay_SPDT_SANYOU_SRD_Series_Form_C
OC1, OC2, OC3, OC4: LTV-817; DIP-4_W10.16mm_LongPads
P1: ISP; IDC-Header_2x05_P2.54mm_Vertical
PS1: RSO-2405S; CONV_RSO-2405S; PARTREV 3
Q1: BC547; TO-92L
Q2: IRFZ24N; TO-220-3_Vertical
R1, R3: 2.5; R_Axial_DIN0922_L20.0mm_D9.0mm_P25.40mm_Horizontal
R2, R17: 10; R_Axial_DIN0207_L6.3mm_D2.5mm_P10.16mm_Horizontal
R4, R16, R18, R19, R22, R23: 10k; R_Axial_DIN0207_L6.3mm_D2.5mm_P10.16mm_Horizontal
R5: 470; R_Axial_DIN0207_L6.3mm_D2.5mm_P10.16mm_Horizontal
R6: 200; R_Axial_DIN0207_L6.3mm_D2.5mm_P10.16mm_Horizontal
R7: 130; R_Axial_DIN0207_L6.3mm_D2.5mm_P10.16mm_Horizontal
R8: 100; R_Axial_DIN0207_L6.3mm_D2.5mm_P10.16mm_Horizontal
R9: 15k; R_Axial_DIN0207_L6.3mm_D2.5mm_P10.16mm_Horizontal
R10: 4k7; R_Axial_DIN0207_L6.3mm_D2.5mm_P10.16mm_Horizontal
R11, R12, R26, R27, R33: 2k2; R_Axial_DIN0207_L6.3mm_D2.5mm_P10.16mm_Horizontal
R13, R14: 1k; R_Axial_DIN0207_L6.3mm_D2.5mm_P10.16mm_Horizontal
R15: 330; R_Axial_DIN0207_L6.3mm_D2.5mm_P10.16mm_Horizontal
R20: nopop; R_Axial_DIN0207_L6.3mm_D2.5mm_P10.16mm_Horizontal
R21, R28: 510; R_Axial_DIN0207_L6.3mm_D2.5mm_P10.16mm_Horizontal
R24, R25: 47k; R_Axial_DIN0207_L6.3mm_D2.5mm_P10.16mm_Horizontal
R29: 20; R_Axial_DIN0207_L6.3mm_D2.5mm_P10.16mm_Horizontal
R30: 150k; R_Axial_DIN0207_L6.3mm_D2.5mm_P10.16mm_Horizontal
R31: 100k; R_Axial_DIN0207_L6.3mm_D2.5mm_P10.16mm_Horizontal
R32: 2k4; R_Axial_DIN0207_L6.3mm_D2.5mm_P10.16mm_Horizontal
RV1: 500k; Potentiometer_Piher_PT-10-V10_Vertical
TP1: GNDD; PinHeader_1x01_P1.00mm_Vertical
TP2: GND-power; PinHeader_1x01_P1.00mm_Vertical
TP3: Driver-in; PinHeader_1x01_P1.00mm_Vertical
TP4: Pedal-in; PinHeader_1x01_P1.00mm_Vertical
TP5: Pedal-filtered; PinHeader_1x01_P1.00mm_Vertical
TP6: BATT; PinHeader_1x01_P1.00mm_Vertical
TP7: OP -; PinHeader_1x01_P1.00mm_Vertical
TP8: OP +; PinHeader_1x01_P1.00mm_Vertical
TP9: OP out; PinHeader_1x01_P1.00mm_Vertical
TP10: SW-filtered; PinHeader_1x01_P1.00mm_Vertical
TP11: SW-in; PinHeader_1x01_P1.00mm_Vertical
U1: LM7818CT; TO-220-3_Vertical
U3: TC429; DIP-8_W7.62mm_Socket_LongPads
U4: LM358N; DIP-8_W7.62mm_LongPads

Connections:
+5V: C6.1, C7.1, C8.1, C16.1, C20.1, IC1.7 (VCC), IC1.20 (AVCC), J6.1, J7.3, J12.1, J13.3, J19.1, P1.2, PS1.6 (+VOUT), R4.1, R16.1, R29.1
+18V: C3.1, C12.1, C13.1, C14.1, C19.1, C21.1, J11.1, R9.1, RV1.1, U1.3 (OUT), U3.1 (Vdd), U3.8 (Vdd), U4.8 (V+)
+24V filtered: C2.1, C4.1, C5.1, C9.1, C10.1, D1.1 (K), D3.2 (A2), D11.1 (K), J10.1, J23.1, J23.2, J24.3, K1.5, PS1.2 (+VIN), R3.2, R18.2, R30.1, U1.1 (IN)
+BATT: F1.1, J1.1, J1.2, J9.1
/BUZZER: IC1.28 ((ADC5/SCL)PC5), R2.2
/LED: IC1.27 ((ADC4/SDA)PC4), R7.2
/LED-ext: IC1.16 ((~SS/OC1B)PB2), R5.1
/MISO: IC1.18 ((MISO)PB4), P1.9
/MOSI: IC1.17 ((MOSI/OC2)PB3), P1.1
/Mosfet (fan): IC1.6 ((XCK/T0)PD4), R28.2
/PWM_0: IC1.15 ((OC1A)PB1), J5.1, R6.1
/RESET: IC1.1 (PC6(~RESET)), P1.5, R4.2
/Relay (light): IC1.5 ((INT1)PD3), R21.2
/SCK: IC1.19 ((SCK)PB5), P1.7
/Switch1: IC1.25 ((ADC2)PC2), R26.2
/Switch2: IC1.26 ((ADC3)PC3), R27.2
/UART_RX: IC1.2 ((RXD)PD0), J16.2
/UART_TX: IC1.3 ((TXD)PD1), J16.1
/analog0 (gas): IC1.24 ((ADC1)PC1), R11.1
/analog1: IC1.23 ((ADC0)PC0), R12.1
/battery-threshold: IC1.4 ((INT0)PD2), R33.1
GND: BZ1.2 (-), C1.2, C6.2, C7.2, C8.2, C11.2, C15.2, C16.2, C17.2, C18.2, C20.2, D4.2 (K), D5.2 (A), D6.2 (A), D12.2 (A), D13.2 (A), IC1.8 (GND), IC1.22 (AGND), J4.1, J4.2, J7.1, J13.1, J16.3, OC1.2, OC2.2, OC3.2, OC4.3, P1.4, P1.6, P1.8, P1.10, PS1.7 (-VOUT), Q1.3 (E), R15.2, R22.2, R23.2, TP1.1
GNDPWR: C2.2, C3.2, C4.2, C5.2, C9.2, C10.2, C12.2, C13.2, C14.2, C19.2, C21.2, D1.2 (A), D3.1 (A1), J2.1, J2.2, J14.2, OC1.3, OC2.3, OC3.3, OC4.2, PS1.1 (-VIN), Q2.3 (S), R10.2, R19.1, R31.2, RV1.3, TP2.1, U1.2 (GND), U3.4 (GND), U3.5 (GND), U4.2 (-), U4.3 (+), U4.4 (V-)
unnamed: BZ1.1 (+), R2.1
unnamed: D4.1 (A), R7.1
unnamed: C1.1, C11.1, D5.1 (K), R11.2, R13.2, TP5.1
unnamed: C15.1, D6.1 (K), J21.1, R12.2, R14.2
unnamed: D9.2 (A), F4.2, J24.1
unnamed: D9.1 (K), J24.2
unnamed: D11.2 (A), K1.2, OC3.4
unnamed: C17.1, D12.1 (K), R24.2, R26.1, TP10.1
unnamed: C18.1, D13.1 (K), R25.2, R27.1
unnamed: F1.2, R1.1, TP6.1
unnamed: F3.1, K1.1
unnamed: IC1.9 (PB6(XTAL1/TOSC1)), R15.1
unnamed: J6.2, R8.1
unnamed: J7.2, R13.1, TP4.1
unnamed: J13.2, R14.1
unnamed: J8.1, J14.1, R17.1, R20.1
unnamed: J17.1, R22.1, R24.1, TP11.1
unnamed: J17.2, R23.1, R25.1
unnamed: J18.1, K1.4
unnamed: F3.2, J18.2
unnamed: J18.3, K1.3
unnamed: J19.2, R29.2
unnamed: OC1.1, R6.2
unnamed: OC2.1, R28.1
unnamed: OC3.1, R21.1
unnamed: OC4.1, R32.2, TP9.1
unnamed: OC4.4, R16.2, R33.2
unnamed: Q1.2 (B), R5.2
unnamed: Q1.1 (C), R8.2
unnamed: F4.1, Q2.2 (D)
unnamed: OC2.4, Q2.1 (G), R18.1, R19.2
unnamed: R1.2, R3.1
unnamed: R17.2, R20.2, U3.6 (OUT), U3.7 (OUT)
unnamed: R32.1, U4.7
unnamed: OC1.4, R9.2, R10.1, TP3.1, U3.2 (INPUT)
unnamed: RV1.2, TP8.1, U4.5 (+)
unnamed: R30.2, R31.1, TP7.1, U4.6 (-)

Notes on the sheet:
ADC Reserve
Batt-voltage threshold signal
ISP Programmer connector
Atmega-8 Microcontroller
Onboard Buzzer and LED
note: its recommended to configure all unused pins as output and set to high at startup to prevent potential noise issues
ADC Gas pedal
Mosfet driver for IGBT
18V needed for mosfet driver
TODO: Add hysteresis?
Power Terminals
24V Supply (voltage filter)
Input voltage range: 20V to 35V
5V Supply (isolated dc-dc converter)
Test-points supplies
18V Supply (linear regulator)
2x Digital input (Switches to 5V)
24V Relay: measured 16.7 mA at 30 V
Short Circuit Protection: continuous, auto recovery
Filter out 50V peaks on battery voltage each pwm cycle
UART connector
gas pedal measurements: 5V-GND: ~1k Ohm when released, ~1k when pressed OUT-GND and OUT-5V: moves between 0.9k to 1.7k
CTRL Pin: high = OFF/low-power open = ON
Input voltage range: 9V to 36V
External LED
Measurements with Optocoupler and 24V relay (15mA) 5 V, 200 Ohm -> I_led = 12 mA 5 V, 510 Ohm -> I_led = 7 mA, U_ce=0.7V 5 V, 820 Ohm -> I_led = 4.5 mA, U_ce=1.8V
Mosfet out (cooling Fan)
Relay for Light

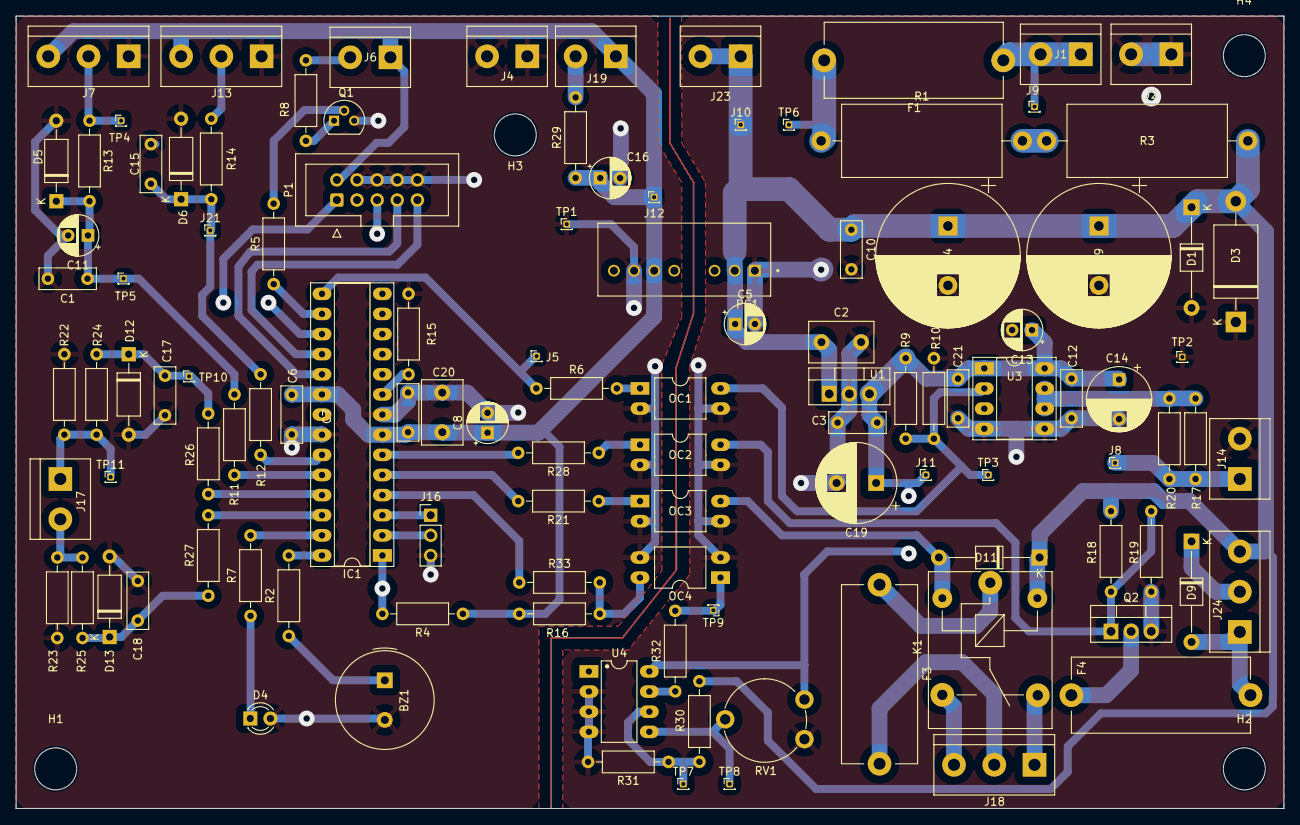
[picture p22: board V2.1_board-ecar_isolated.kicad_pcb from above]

Board: 4 copper layers, 160.0 x 100.0 mm, 116 parts (0 on the bottom side), 60 nets.

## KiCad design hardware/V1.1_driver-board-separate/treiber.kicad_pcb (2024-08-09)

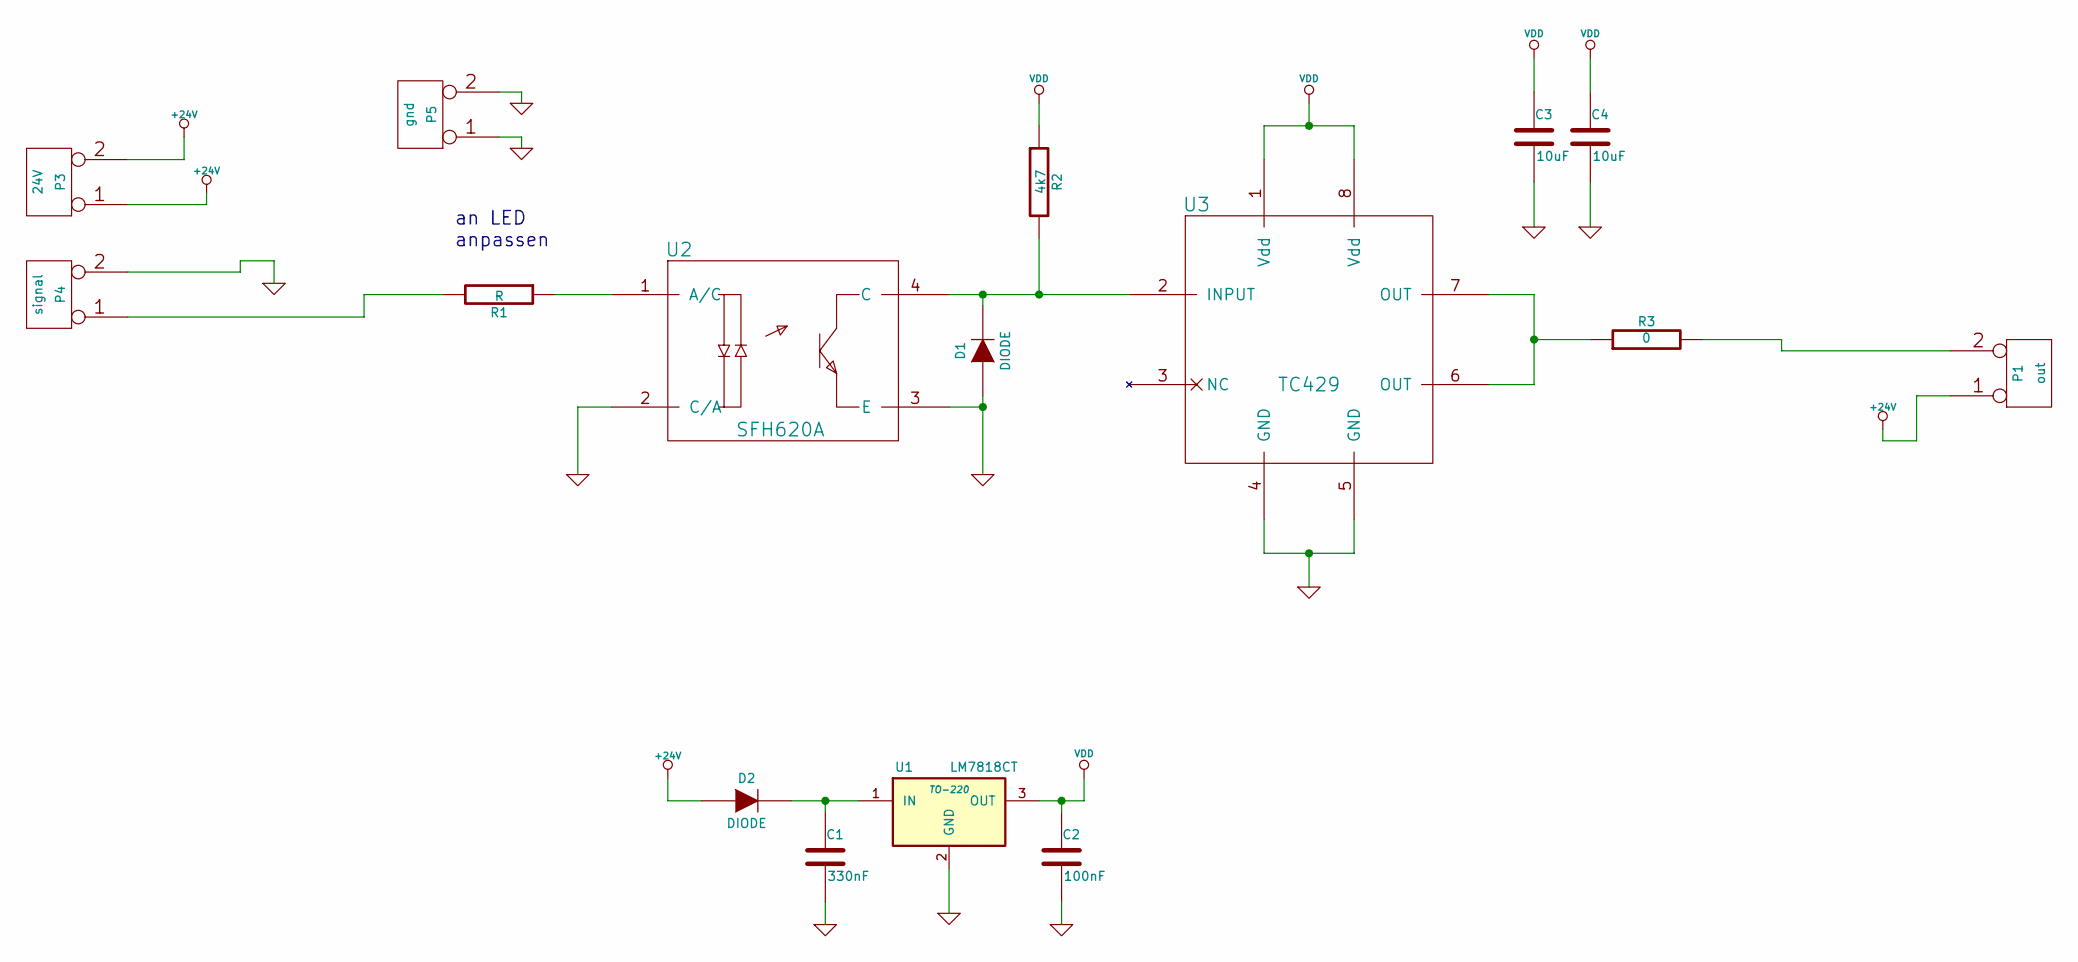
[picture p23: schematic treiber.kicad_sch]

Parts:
C1: 330nF
C2: 100nF
C3, C4: 10uF
D1, D2: DIODE
P1: out
P3: 24V
P4: signal
P5: gnd
R1: R
R2: 4k7
R3: 0
U1: LM7818CT; TO-220
U2: SFH620A
U3: TC429

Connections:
+24V: D2.1 (A), P1.1, P3.1, P3.2 (PM)
GND: C1.2, C2.2, C3.2, C4.2, D1.1 (A), P4.2 (PM), P5.1, P5.2 (PM), U1.2 (GND), U2.2 (C/A), U2.3 (E), U3.4 (GND), U3.5 (GND)
unnamed: P4.1, R1.2
unnamed: P1.2 (PM), R3.2
unnamed: R3.1, U3.6 (OUT), U3.7 (OUT)
unnamed: C1.1, D2.2 (K), U1.1 (IN)
unnamed: D1.2 (K), R2.2, U2.4 (C), U3.2 (INPUT)
unnamed: R1.1, U2.1 (A/C)
VDD: C2.1, C3.1, C4.1, R2.1, U1.3 (OUT), U3.1 (Vdd), U3.8 (Vdd)

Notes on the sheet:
an LED anpassen

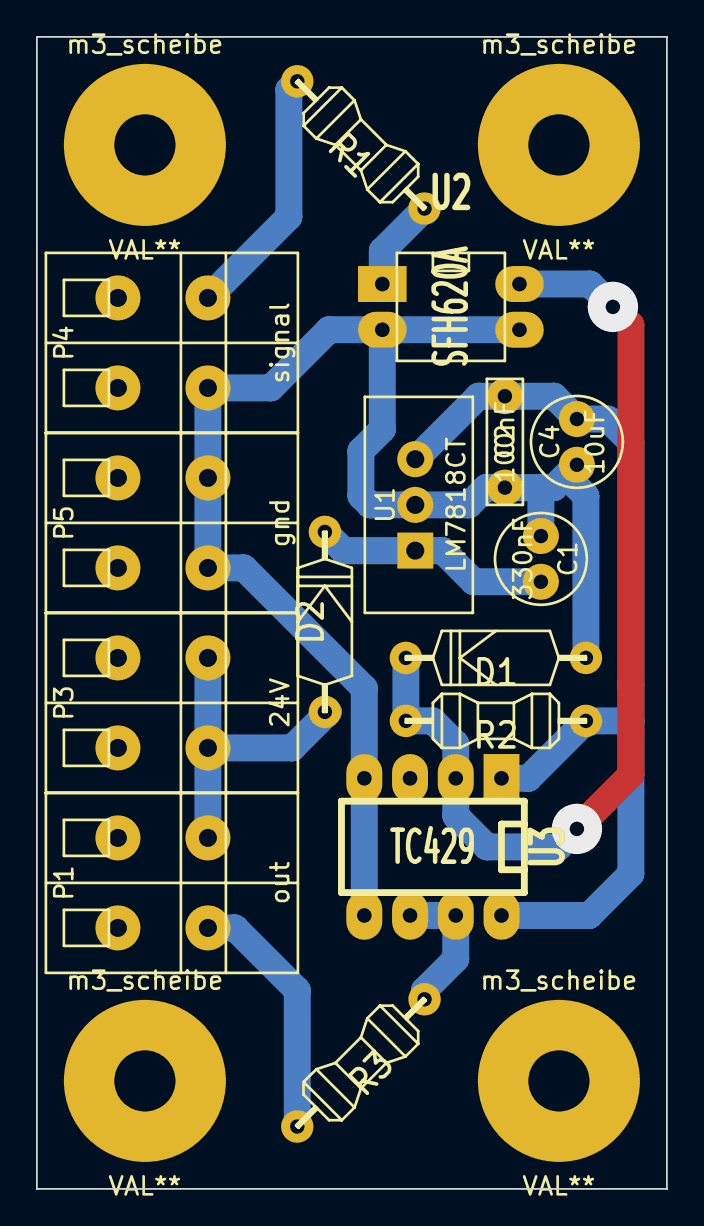
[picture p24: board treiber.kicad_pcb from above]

Board: 2 copper layers, 35.0 x 64.0 mm, 19 parts (0 on the bottom side), 9 nets.

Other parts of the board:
m3_scheibe, m3_scheibe#2, m3_scheibe#3, m3_scheibe#4: VAL**; m3_scheibe

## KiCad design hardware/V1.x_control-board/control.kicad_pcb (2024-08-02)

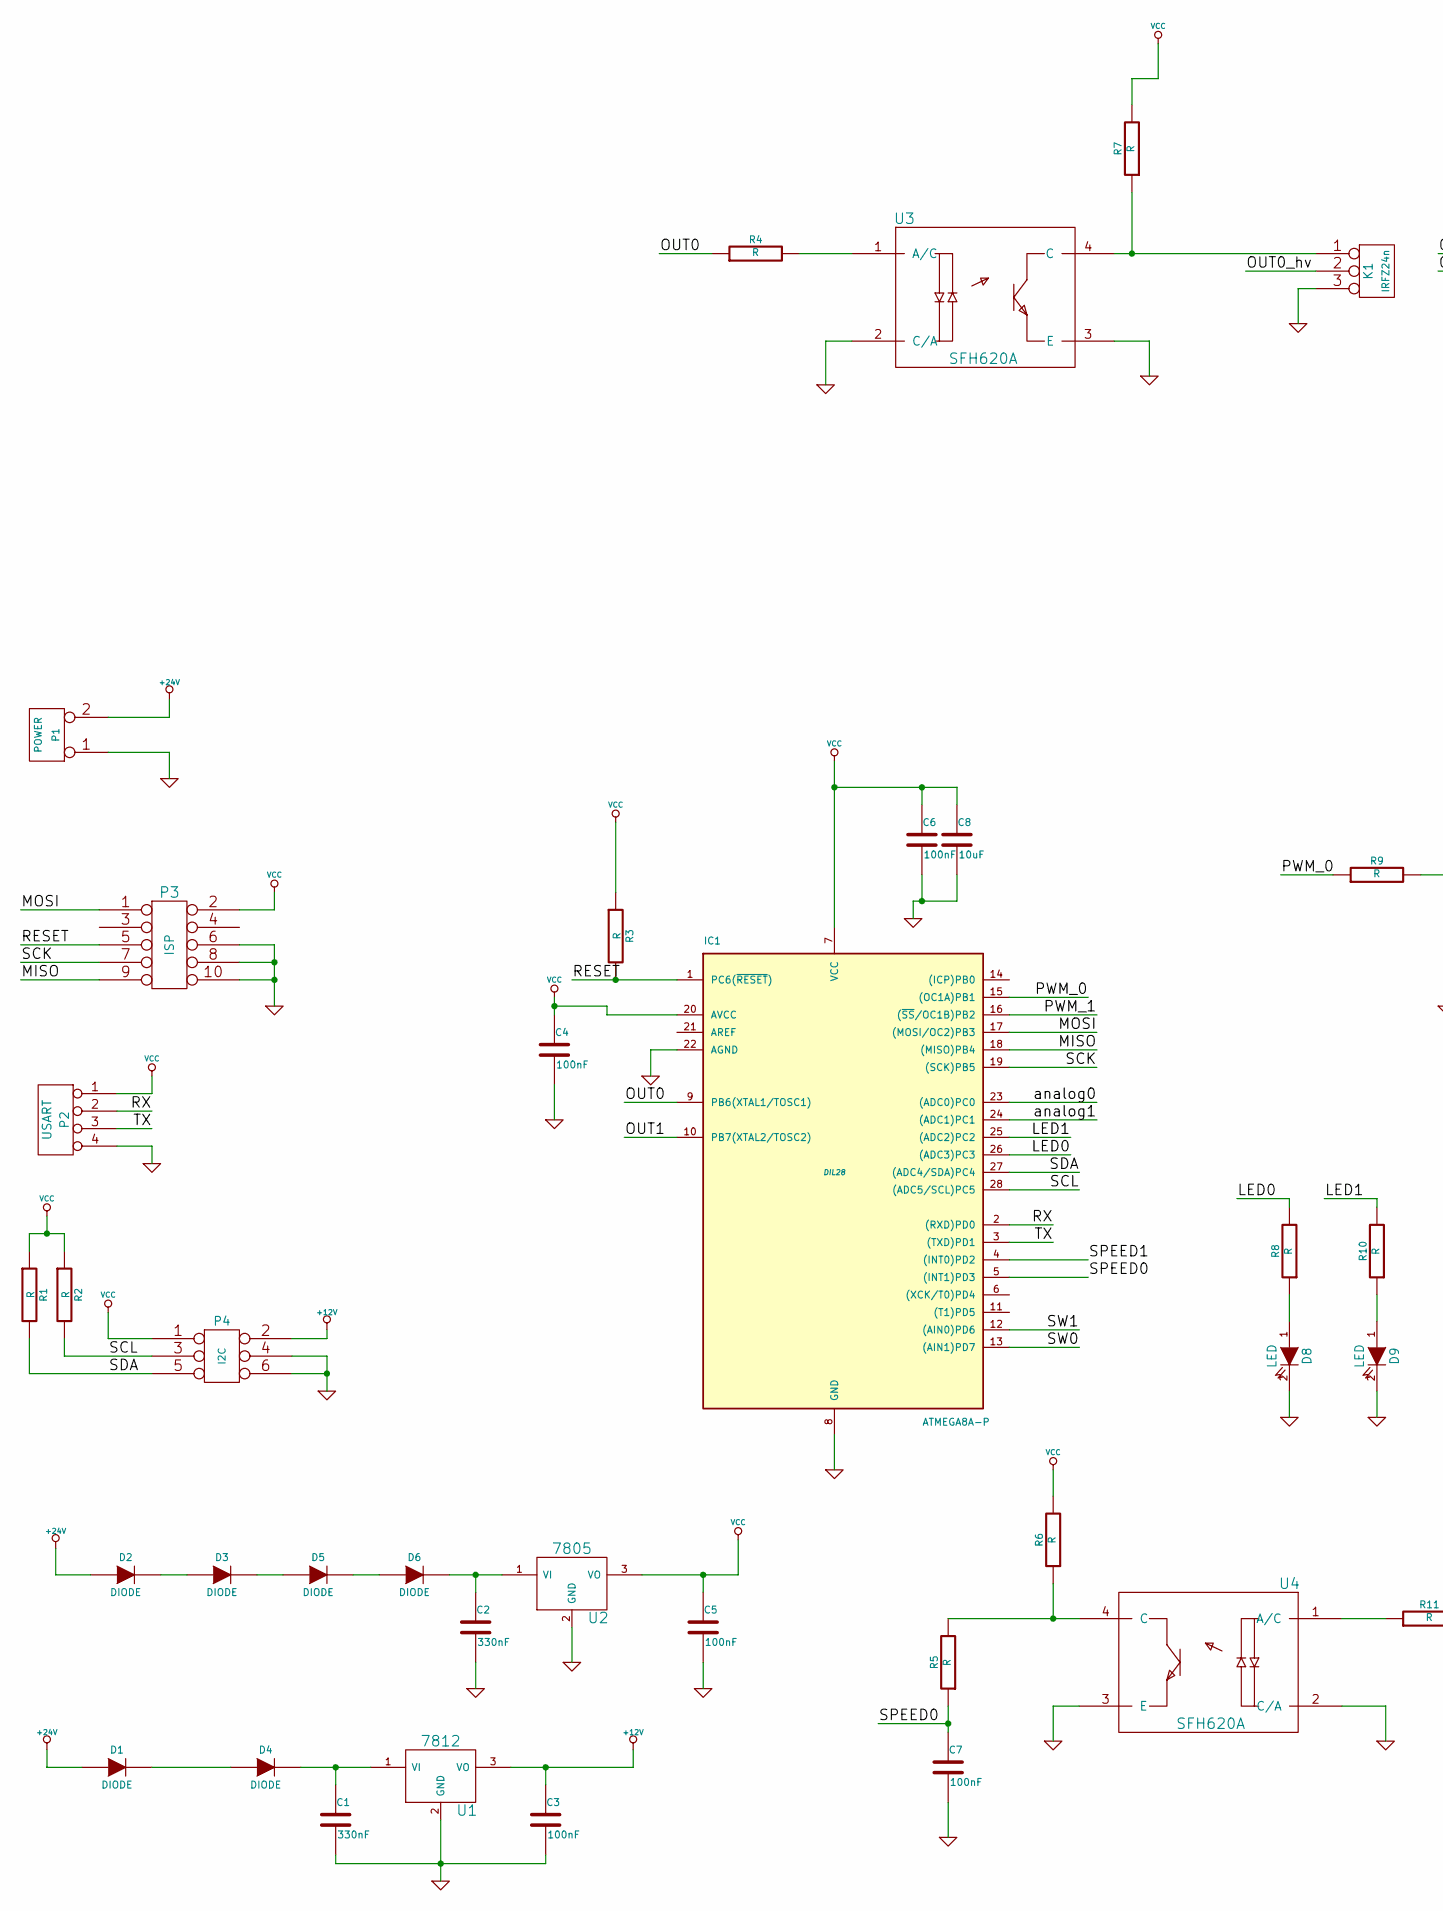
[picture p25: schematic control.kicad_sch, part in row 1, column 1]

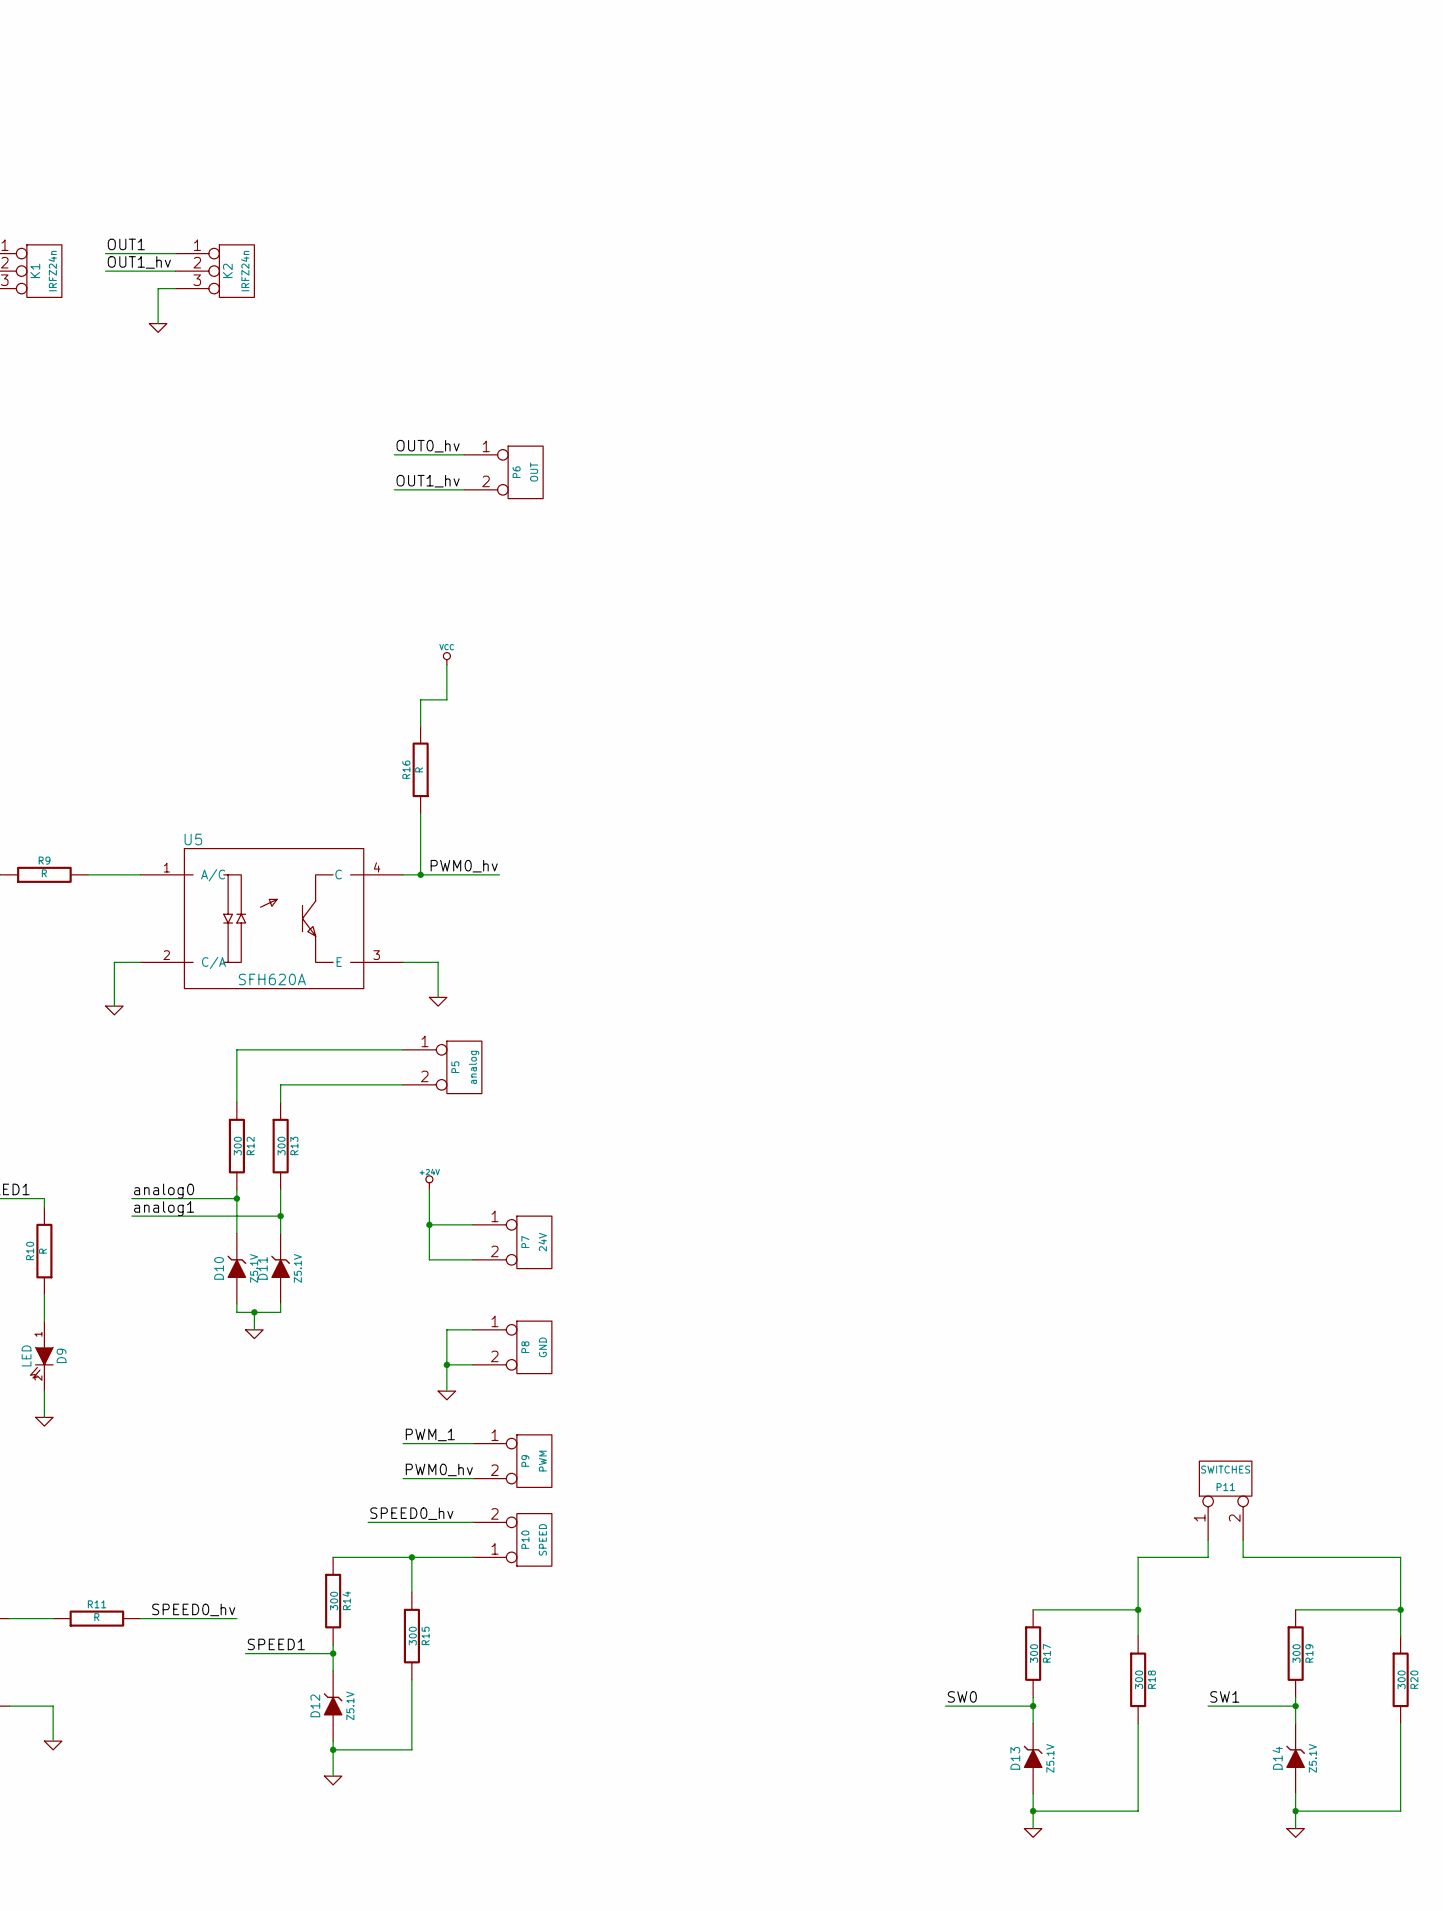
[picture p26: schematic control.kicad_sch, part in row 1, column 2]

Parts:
C1, C2: 330nF
C3, C4, C5, C6, C7: 100nF
C8: 10uF
D1, D2, D3, D4, D5, D6: DIODE
D8, D9: LED
D10, D11, D12, D13, D14: Z5.1V
IC1: ATMEGA8A-P; DIL28
K1, K2: IRFZ24n
P1: POWER
P2: USART
P3: ISP
P4: I2C
P5: analog
P6: OUT
P7: 24V
P8: GND
P9: PWM
P10: SPEED
P11: SWITCHES
R1, R2, R3, R4, R5, R6, R7, R8, R9, R10, R11, R16: R
R12, R13, R14, R15, R17, R18, R19, R20: 300
U1: 7812
U2: 7805
U3, U4, U5: SFH620A

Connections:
+12V: C3.1, P4.2, U1.3 (VO)
+24V: D1.1 (A), D2.1 (A), P1.2 (PM), P7.1, P7.2 (PM)
/LED0: IC1.26 ((ADC3)PC3), R8.2
/LED1: IC1.25 ((ADC2)PC2), R10.2
/MISO: IC1.18 ((MISO)PB4), P3.9
/MOSI: IC1.17 ((MOSI/OC2)PB3), P3.1
/OUT0: IC1.9 (PB6(XTAL1/TOSC1)), R4.1
/OUT0_hv: K1.2 (PM), P6.1
/OUT1: IC1.10 (PB7(XTAL2/TOSC2)), K2.1
/OUT1_hv: K2.2 (PM), P6.2 (PM)
/PWM0_hv: P9.2 (PM), R16.1, U5.4 (C)
/PWM_0: IC1.15 ((OC1A)PB1), R9.1
/PWM_1: IC1.16 ((~SS/OC1B)PB2), P9.1
/RESET: IC1.1 (PC6(~RESET)), P3.5, R3.2
/RX: IC1.2 ((RXD)PD0), P2.2
/SCK: IC1.19 ((SCK)PB5), P3.7
/SCL: IC1.28 ((ADC5/SCL)PC5), P4.3, R2.2
/SDA: IC1.27 ((ADC4/SDA)PC4), P4.5, R1.2
/SPEED0: C7.1, IC1.5 ((INT1)PD3), R5.1
/SPEED0_hv: P10.2 (PM), R11.2
/SPEED1: D12.2 (K), IC1.4 ((INT0)PD2), R14.2
/SW0: D13.2 (K), IC1.13 ((AIN1)PD7), R17.2
/SW1: D14.2 (K), IC1.12 ((AIN0)PD6), R19.2
/TX: IC1.3 ((TXD)PD1), P2.3
/analog0: D10.2 (K), IC1.23 ((ADC0)PC0), R12.2
/analog1: D11.2 (K), IC1.24 ((ADC1)PC1), R13.2
GND: C1.2, C2.2, C3.2, C4.2, C5.2, C6.2, C7.2, C8.2, D8.2 (K), D9.2 (K), D10.1 (A), D11.1 (A), D12.1 (A), D13.1 (A), D14.1 (A), IC1.8 (GND), IC1.22 (AGND), K1.3, K2.3, P1.1, P2.4, P3.6, P3.8, P3.10, P4.4, P4.6, P8.1, P8.2 (PM), R15.2, R18.2, R20.2, U1.2 (GND), U2.2 (GND), U3.2 (C/A), U3.3 (E), U4.2 (C/A), U4.3 (E), U5.2 (C/A), U5.3 (E)
unnamed: P11.2 (PM), R19.1, R20.1
unnamed: P11.1, R17.1, R18.1
unnamed: R5.2, R6.1, U4.4 (C)
unnamed: R11.1, U4.1 (A/C)
unnamed: P5.1, R12.1
unnamed: P5.2 (PM), R13.1
unnamed: K1.1, R7.1, U3.4 (C)
unnamed: R4.2, U3.1 (A/C)
unnamed: D8.1 (A), R8.1
unnamed: D9.1 (A), R10.1
unnamed: P10.1, R14.1, R15.1
unnamed: R9.2, U5.1 (A/C)
unnamed: D1.2 (K), D4.1 (A)
unnamed: C1.1, D4.2 (K), U1.1 (VI)
unnamed: D5.2 (K), D6.1 (A)
unnamed: D2.2 (K), D3.1 (A)
unnamed: D3.2 (K), D5.1 (A)
unnamed: C2.1, D6.2 (K), U2.1 (VI)
VCC: C4.1, C5.1, C6.1, C8.1, IC1.7 (VCC), IC1.20 (AVCC), P2.1, P3.2, P4.1, R1.1, R2.1, R3.1, R6.2, R7.2, R16.2, U2.3 (VO)

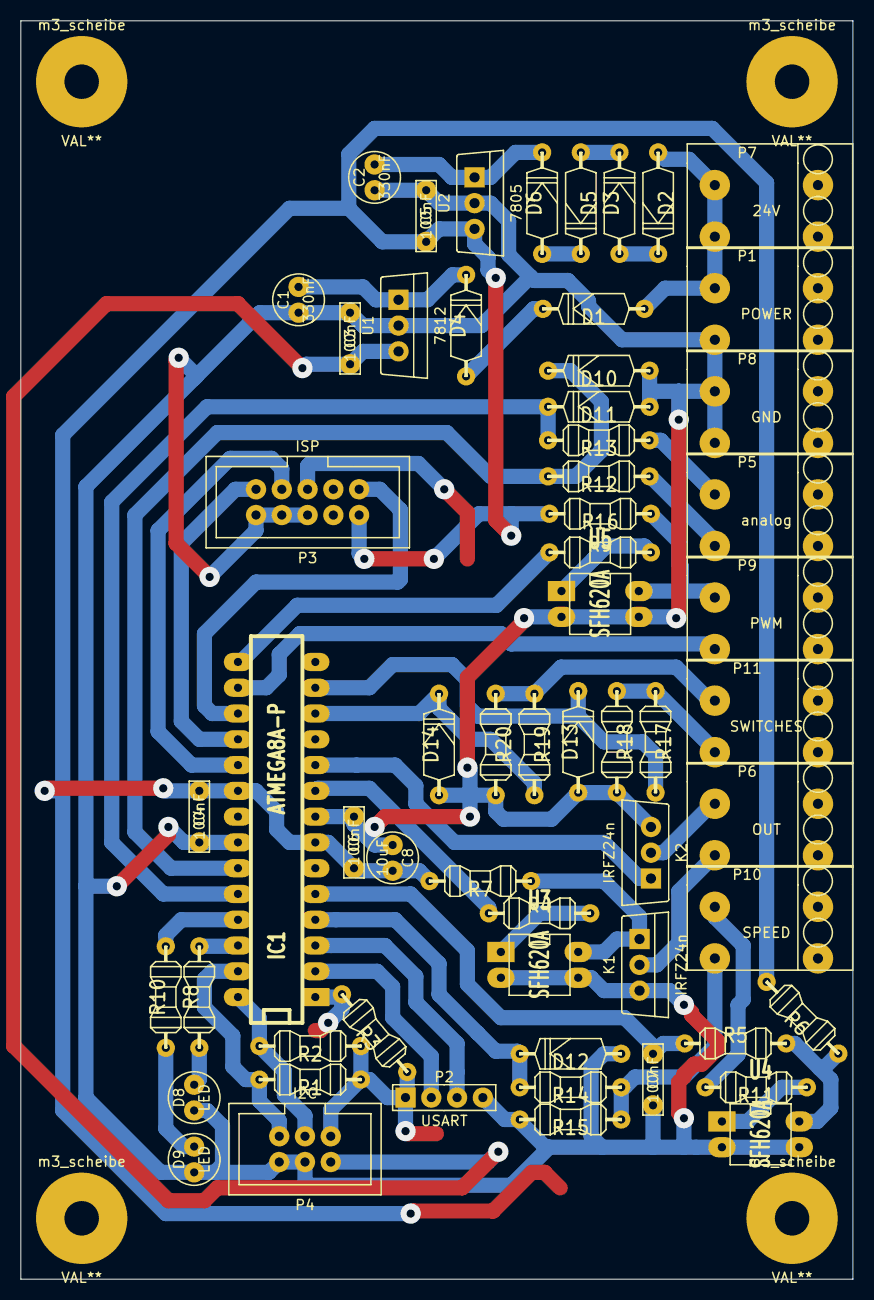
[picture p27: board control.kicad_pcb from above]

Board: 2 copper layers, 82.0 x 124.0 mm, 64 parts (0 on the bottom side), 46 nets.

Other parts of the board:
m3_scheibe, m3_scheibe#2, m3_scheibe#3, m3_scheibe#4: VAL**; m3_scheibe

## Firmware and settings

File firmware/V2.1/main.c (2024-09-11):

#include <util/delay.h>
#include <avr/wdt.h>
#include "usart.h"
#include "adc.h"
#include "gpio.h"
#include "time.h"
#include "buzzer.h"
#include "pwm.h"


//====================
//==== PWM-config ====
//====================
//Pre-calculated possible combinations:
/*
|  Resolution  |  Prescaler  |  PWM-Freq @ 8MHz  |  Comment  |
1023	  1	      7813      (2) >> OK - minor beeping, temperature just fine with fan on
1023	  8	      977       (5) >> still beeping, a little less annoying than 2kHz (4)
1023	  64	    122       (8) <== used in V1 ==> loud humming and metal vibrations
1023	  256	    31
1023	  1024	  8
		
511	    1	      15625     (1) >> OK - no sound at all, but IGBT gets VERY-HOT in seconds
511	    8	      1953      (4) >> annoying beeping, similar to 3.9kHz (3)
511	    64	    244       (7) >> OK - quieter than V1.0 122Hz (8)
511	    256	    61
511	    1024	  15
		
255	    1	      31250
255	    8	      3906      (3) >> very annoying/loud beeping
255	    64	    488       (6) >> annoying low beep
255	    256	    122
255	    1024  	31
*/

// struct that configures PWM and fan settings
typedef struct
{
  // Maximum count value for Fast PWM
  // Possible values: 1023(10Bit), 511(9Bit), 255(8Bit)
  uint16_t pwmResolution;

  // Factor clock is reduced before counting up the value
  // Possible values: 1, 8, 64, 256, 1024
  uint16_t pwmPrescaler;

  // switch to default config when motor is continuously on longer than that (prevent overheating)
  uint32_t maxTimeOnContinuous;

  uint32_t fanTurnOffDelay;
  uint32_t fanTurnOnDelay;
  uint32_t fanTurnOnDuty;
} ekartConfig_t;


// define multiple config presets, those can be switched between / selected at runtime with the button
ekartConfig_t configs[] = {
      { //61 Hz []
        .pwmResolution = 511,
        .pwmPrescaler = 256,
        .maxTimeOnContinuous = 0,
        .fanTurnOffDelay = 10000,
        .fanTurnOnDelay = 2000,
        .fanTurnOnDuty = 10
    },
      { //122 Hz (V1) []
        .pwmResolution = 1023,
        .pwmPrescaler = 64,
        .maxTimeOnContinuous = 0,
        .fanTurnOffDelay = 10000,
        .fanTurnOnDelay = 2000,
        .fanTurnOnDuty = 10
    },
        { //244 Hz
        .pwmResolution = 511,
        .pwmPrescaler = 64,
        .maxTimeOnContinuous = 0,
        .fanTurnOffDelay = 15000,
        .fanTurnOnDelay = 2000,
        .fanTurnOnDuty = 10
    },
        { //488 Hz []
        .pwmResolution = 255,
        .pwmPrescaler = 64,
        .maxTimeOnContinuous = 0,
        .fanTurnOffDelay = 15000,
        .fanTurnOnDelay = 2000,
        .fanTurnOnDuty = 10
    },
      { //977 Hz []
        .pwmResolution = 1023,
        .pwmPrescaler = 8,
        .maxTimeOnContinuous = 0,
        .fanTurnOffDelay = 20000,
        .fanTurnOnDelay = 2000,
        .fanTurnOnDuty = 10
    },
      { //1.9 kHz []
        .pwmResolution = 511,
        .pwmPrescaler = 8,
        .maxTimeOnContinuous = 0,
        .fanTurnOffDelay = 20000,
        .fanTurnOnDelay = 2000,
        .fanTurnOnDuty = 10
    },
      { //3.9 kHz []
        .pwmResolution = 255,
        .pwmPrescaler = 8,
        .maxTimeOnContinuous = 0,
        .fanTurnOffDelay = 20000,
        .fanTurnOnDelay = 1000,
        .fanTurnOnDuty = 0
    },
      { //7.8 kHz (default)
        .pwmResolution = 1023,
        .pwmPrescaler = 1,
        .maxTimeOnContinuous = 15000,
        .fanTurnOffDelay = 20000,
        .fanTurnOnDelay = 1000,
        .fanTurnOnDuty = 0
    },
      { //15.6 kHz (note: too fast in low duty - never off in cycle, gets hot fast)
        .pwmResolution = 511,
        .pwmPrescaler = 1,
        .maxTimeOnContinuous = 6000,
        .fanTurnOffDelay = 50000,
        .fanTurnOnDelay = 500,
        .fanTurnOnDuty = 0
    },
};

uint8_t configCount = sizeof(configs)/sizeof(ekartConfig_t);
// default config
#define DEFAULT_CONFIG_INDEX 2 // = 244Hz
uint8_t selectedConfigIndex = DEFAULT_CONFIG_INDEX; // <== set default config



//====================
//====== config ======
//====================
#define GAS_PEDAL_MIN 90 // actual 82
#define GAS_PEDAL_MAX 542 //actual 543

#define DUTY_PERCENT_SLOW_MODE 45 //max duty percent in slow mode (long button press)

#define DEBUG_OUTPUT_ENABLED 0 // when set to 1: output e.g. adc, duty, gaspedal... via uart

#define TIMEOUT_NOTIFY_INACTIVITY (uint32_t)5*60*60*1000 //5h (notify "forgot to turn off")
#define INACTIVITY_CHECK_INTERVAL (uint32_t)45*1000 //interval buzzer beeps when idle too long



//===============================
//===== Configure GPIO Pins =====
//===============================
//outputs
const GPIO_Pin relay = { PD3, &PORTD, &DDRD, &PIND };
const GPIO_Pin pwm = {PB1, &PORTB, &DDRB, &PINB};
const GPIO_Pin fan = {PD4, &PORTD, &DDRD, &PIND};
const GPIO_Pin ledOnboard = {PC4, &PORTC, &DDRC, &PINC};
const GPIO_Pin ledExternal = {PB2, &PORTB, &DDRB, &PINB};
const GPIO_Pin buzzerPin = {PC5, &PORTC, &DDRC, &PINC};

//inputs
const GPIO_Pin toggleSwitch = {PC2, &PORTC, &DDRC, &PINC};
const GPIO_Pin button = {PC3, &PORTC, &DDRC, &PINC};
const GPIO_Pin analog = {PC0, &PORTC, &DDRC, &PINC};
const GPIO_Pin gasPedal = {PC1, &PORTC, &DDRC, &PINC};
const GPIO_Pin batteryThreshold = {PD2, &PORTD, &DDRD, &PIND};

//Initialize Pins (define direction)
void init_gpios(){
  //outputs
  GPIO_Init(&relay, 1);
  GPIO_Init(&pwm, 1);
  GPIO_Init(&fan, 1);
  GPIO_Init(&ledOnboard, 1);
  GPIO_Init(&ledExternal, 1);
  GPIO_Init(&buzzerPin, 1);
  // inputs
  GPIO_Init(&toggleSwitch, 0);
  GPIO_Init(&button, 0);
  GPIO_Init(&analog, 0);
  GPIO_Init(&gasPedal, 0);
  GPIO_Init(&batteryThreshold, 0);
}


// configure buzzer object
buzzerConfig_t buzzer = {
    .pin = buzzerPin,
    .msOn = 60,
    .msOff = 100,
    .msLong = 800,
    .isOn = 0,
    .countRemainingLong = 0,
    .countRemaining = 0,
    .timestamp_turnedOn = 0,
    .timestamp_turnedOff = 0
};






//=====================
//===== functions =====
//=====================
// initialize pwm with currently selected configuration and handle error
void emablePwmWithConfig(){
  int res = pwm_initFastPwmTimer1(configs[selectedConfigIndex].pwmResolution, configs[selectedConfigIndex].pwmPrescaler);
  if (res){
    printf("==== ERROR: PWM INIT FAILED! invalid parameter provided config_index=%d ====", selectedConfigIndex);
    GPIO_Set(&buzzerPin);
    _delay_ms(3000);
    GPIO_Clear(&buzzerPin);
    //trigger reset
    wdt_enable(WDTO_15MS);
  }
}



typedef enum {FULL_OFF = 0, FULL_ON, PWM} motorState_t;
const char* motorState_str[] = {"FULL_OFF", "FULL_ON", "PWM"};





//======================
//======== main ========
//======================
int main(void)
{
  // init PWM
  emablePwmWithConfig(); // init and test if config is valid
  pwm_disable(); // initially off

  // init adc
  ADC_Init();

  // init gpio
  init_gpios();
  GPIO_Set(&fan); //turn off fan initially

  // init Timer2+ISR that tracks time in ms for time_ functions
  time_init();

  // beep after startup
  buzzer_beep(&buzzer, 3);

  // init UART
  uart_init();
  uart_sendStr("startup finished\n");
  printf("CPU Frequency is %ld Hz\n", F_CPU);


  //==== variables ====
  // motor:
  uint32_t gasPedalAdc;
  uint8_t pwmEnabled = 0;
  motorState_t state = FULL_OFF;
  motorState_t statePrev = FULL_OFF;
  uint16_t duty = 0;
  uint32_t timestamp_turnedOn = 0;
  uint32_t timestamp_turnedOff = 0;
  // edge detection:
  uint8_t buttonPrevious = 0;
  uint32_t timestamp_buttonPressed = 0;
  // inactivity beep:
  uint32_t timestamp_lastActivity = 0;
  uint32_t timestamp_lastInactivityCheck = 0;
  // slow mode:
  uint16_t maxDutyPercent = 100;
  uint8_t lock = 0;


  //==== loop ====
  while (1)
  {

    // handle buzzer (handle beeping without blocking the loop)
    buzzer_handle(&buzzer);

    //load currently selected config
    ekartConfig_t conf = configs[selectedConfigIndex];


    // read gas pedal
    gasPedalAdc = ADC_ReadChannel(gasPedal.bit);


    //=== motor control ===
    if (gasPedalAdc <= GAS_PEDAL_MIN) // pedal released
    {
      state = FULL_OFF;
      // turn off pwm for complete stop
      if (pwmEnabled)
      { 
        pwm_disable();
        pwmEnabled = 0;
        timestamp_turnedOff = time_get_ms();
      }
      // set pin constantly low = full off
      GPIO_Clear(&pwm);
    }
    else if ((gasPedalAdc >= GAS_PEDAL_MAX) && (maxDutyPercent == 100)) // pedal fully pressed
    {
      state = FULL_ON;
      // turn off pwm for full on
      if (pwmEnabled)
      {
        pwm_disable();
        pwmEnabled = 0;
      }
      // set pin constantly high = full on
      GPIO_Set(&pwm);
    }
    else // pedal anywhere between min/max
    {
      state = PWM;
      if (!pwmEnabled)
      { // re-enable pwm if previously off
        emablePwmWithConfig();
        pwmEnabled = 1;
        timestamp_turnedOn = time_get_ms();
      }
      // define duty
      // scale pedal input to pwm value
      duty = (gasPedalAdc - GAS_PEDAL_MIN) * conf.pwmResolution * maxDutyPercent / 100 / (GAS_PEDAL_MAX - GAS_PEDAL_MIN);

      // update duty
      pwm_setDutyCycle(duty);
    }


    //=== logging ===
    // debug output via UART
    #if DEBUG_OUTPUT_ENABLED == 1
    //note: for some reason wrong values are printed when printing multiple variables in on printf?!
    printf("adc=%04d", gasPedalAdc); 

    printf(" pedal=%04d/1000",
      (int32_t)(gasPedalAdc - GAS_PEDAL_MIN) * 1000 / (GAS_PEDAL_MAX - GAS_PEDAL_MIN));

    printf(" pwm=%04d/%d", duty, conf.pwmResolution);
    
    printf(" state='%s'", motorState_str[(int)state]);

    printf("freq=%dHz\n", PWM_FREQUENCY(conf.pwmPrescaler, conf.pwmResolution));

    #endif


    //=== onboard LED ===
    // on when motor is running
    GPIO_SetLevel(&ledOnboard, (gasPedalAdc >= GAS_PEDAL_MIN));


    //=== external LED ===
    // always on except when buzzer is on (also have optical notification)
    if (GPIO_Read(&buzzerPin) == 1)
      GPIO_Clear(&ledExternal);
    else
      GPIO_Set(&ledExternal);



    //=== fan ===
    // note: output is inverted
    // turn fan on when motor on and above thresholds
    uint32_t timeOn = time_msPassedSince(timestamp_turnedOn);
    if (state != FULL_OFF &&  (duty >= conf.fanTurnOnDuty) && ((time_msPassedSince(timestamp_turnedOn)) > conf.fanTurnOnDelay))
      GPIO_Clear(&fan); // turn on

    // turn fan off when motor off long enough
    else if (state == FULL_OFF && (time_msPassedSince(timestamp_turnedOff) > conf.fanTurnOffDelay))
      GPIO_Set(&fan); // turn off

    // printf("time=%d, ", time);
    // printf("turnedon=%d", timestamp_turnedOn);
    // printf("timeon=%d\n", timeOn);
    //  manual control via switch near emergency stop
    //  GPIO_SetLevel(&fan, !(GPIO_Read(&button)));



    //=== Switch, Relay ===
    // on when switch is high (currently not connected)
    GPIO_SetLevel(&relay, GPIO_Read(&toggleSwitch));


    //==== handle Button ====
    uint8_t buttonNow = GPIO_Read(&button);
    uint32_t timePressed = time_msPassedSince(timestamp_buttonPressed); //TODO: only calculate this when switchLast is 1 otherwise 0 and reset lock?

    if (buttonPrevious == 0 && buttonNow == 1) // rising edge
    {
      timestamp_buttonPressed = time_get_ms();
    }

    else if (buttonPrevious == 1 && buttonNow == 0) // falling edge
    {
      if (timePressed < 1000) //short press
      {
        //--- cycle through configs ---
        selectedConfigIndex++;
        if (selectedConfigIndex >= configCount) // rotate back first index
          selectedConfigIndex = 0;
        // re-configure pwm immediately when active
        if (pwmEnabled){
          pwm_setDutyCycle(0); // set to low duty for this cycle
          emablePwmWithConfig(); // re-initialize with new settings
        }
        timestamp_turnedOn = time_get_ms(); // reset motor on-time (for config maxOnTime)
        printf("cycled config index to %d", selectedConfigIndex);
        buzzer_beep(&buzzer, 2);
      }
    }

    else if ((buttonNow == 1 && timePressed > 1000) && !lock) //long press
    {
      //--- toggle slow mode ---
      if (maxDutyPercent != 100) // enter normal mode (full speed)
      {
        maxDutyPercent = 100;
        buzzer_beepLong(&buzzer, 1);
      }
      else  //enter slow mode
      {
        maxDutyPercent = DUTY_PERCENT_SLOW_MODE;
        buzzer_beepLong(&buzzer, 2);
      }
      lock = 1; // prevent multiple runs while still pressed
    }
    else if (buttonNow == 0) // released
    {
      lock = 0; // reset long pressed lock
    }

    // update previous switch state
    buttonPrevious = buttonNow;


    //=== handle config auto-exit condition ===
    // switch config in case time restriction is configured and exceeded
    if (conf.maxTimeOnContinuous > 0 && state != FULL_OFF && (time_msPassedSince(timestamp_turnedOn) > conf.maxTimeOnContinuous))
    {
      selectedConfigIndex = DEFAULT_CONFIG_INDEX;
      // re-configure pwm immediately when active
      if (pwmEnabled)
      {
        pwm_setDutyCycle(0);   // set to low duty for this cycle
        emablePwmWithConfig(); // re-initialize with new settings
      }
      buzzer_beepLong(&buzzer, 2);
    }


    //=== Voltage-Threshold ===
    //beep when battery below voltage threshold (opamp+potentiometer)
    //pass through batt threshold signal to buzzer (testing):
    //GPIO_SetLevel(&buzzer, !(GPIO_Read(&batteryThreshold)));

    //when below voltage threshold: beep every time when pedal gets released
    if (statePrev == PWM && state == FULL_OFF && !(GPIO_Read(&batteryThreshold))) // pedal just fully released and battery low
      buzzer_beepLong(&buzzer, 1);


    //=== inactivity check ===
    // track last activity
    if (state == FULL_ON && statePrev != FULL_ON) // motor just changed to full-on (counts as activity)
      timestamp_lastActivity = time_get_ms();
    // repeatedly check and beep if inactivity threshold is exceeded
    // TODO put this check in a slow loop
    if ((time_msPassedSince(timestamp_lastInactivityCheck) > INACTIVITY_CHECK_INTERVAL) //check is due
    && (time_msPassedSince(timestamp_lastActivity) > TIMEOUT_NOTIFY_INACTIVITY)){ // inactive long enough
      buzzer_beepLong(&buzzer, 2);
      timestamp_lastInactivityCheck = time_get_ms();
    }


    // update last motor state
    statePrev = state;
    _delay_ms(1);
  }
}

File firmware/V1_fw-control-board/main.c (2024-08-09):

#include <avr/io.h>
#include <util/delay.h>
#include <stdio.h>
#include "usart.h"
#include "display.h"

// define the PWM clock divider. The PWM frequency will be
// F_PWM = F_CPU / PWM_CLOCKDIV
// F_CPU has to be defined in the makefile, and make fuse
// has to be executed for changes of F_CPU to get effective
// Possible values for PWM_CLOCKDIV are
// 1024, 8192, 65536, 262144

//#define PWM_CLKDIV 1024     // presc 1
//#define PWM_CLKDIV 8192     // presc 8
#define PWM_CLKDIV 65536    // presc 64
//#define PWM_CLKDIV 262144   // presc 256


// PWM0 (output)
#define PWM0 PB1
#define PWM0_PORT PORTB
#define PWM0_DDR DDRB
#define PWM0_PIN PINB
#define SET_PWM0 (PWM0_PORT |= (1<<PB1))
#define CLEAR_PWM0 (PWM0_PORT &= ~(1<<PB1))

// PWM1 (output)
#define PWM1 PB2
#define PWM1_PORT PORTB
#define PWM1_DDR DDRB
#define PWM1_PIN PINB
#define SET_PWM1 (PWM1_PORT |= (1<<PB2))
#define CLEAR_PWM1 (PWM1_PORT &= ~(1<<PB2))

// OUT0 (output)
#define OUT0 PB6
#define OUT0_PORT PORTB
#define OUT0_DDR DDRB
#define OUT0_PIN PINB
#define SET_OUT0 (OUT0_PORT |= (1<<PB6))
#define CLEAR_OUT0 (OUT0_PORT &= ~(1<<PB6))

// OUT2 (output)
#define OUT2 PB7
#define OUT2_PORT PORTB
#define OUT2_DDR DDRB
#define OUT2_PIN PINB
#define SET_OUT2 (OUT2_PORT |= (1<<PB7))
#define CLEAR_OUT2 (OUT2_PORT &= ~(1<<PB7))

// ANALOG0 (input)
#define ANALOG0 PC0
#define ANALOG0_PORT PORTC
#define ANALOG0_DDR DDRC
#define ANALOG0_PIN PINC
#define IS_HIGH_ANALOG0 (ANALOG0_PIN & (1<<PC0))
#define SET_PULLUP_ANALOG0 (ANALOG0_PORT |= (1<<PC0))
#define CLEAR_PULLUP_ANALOG0 (ANALOG0_PORT &= ~(1<<PC0))

// ANALOG1 (input)
#define ANALOG1 PC1
#define ANALOG1_PORT PORTC
#define ANALOG1_DDR DDRC
#define ANALOG1_PIN PINC
#define IS_HIGH_ANALOG1 (ANALOG1_PIN & (1<<PC1))
#define SET_PULLUP_ANALOG1 (ANALOG1_PORT |= (1<<PC1))
#define CLEAR_PULLUP_ANALOG1 (ANALOG1_PORT &= ~(1<<PC1))

// LED1 (output)
#define LED1 PC2
#define LED1_PORT PORTC
#define LED1_DDR DDRC
#define LED1_PIN PINC
#define SET_LED1 (LED1_PORT |= (1<<PC2))
#define CLEAR_LED1 (LED1_PORT &= ~(1<<PC2))

// LED0 (output)
#define LED0 PC3
#define LED0_PORT PORTC
#define LED0_DDR DDRC
#define LED0_PIN PINC
#define SET_LED0 (LED0_PORT |= (1<<PC3))
#define CLEAR_LED0 (LED0_PORT &= ~(1<<PC3))

// SPEED1 (input)
#define SPEED1 PD2
#define SPEED1_PORT PORTD
#define SPEED1_DDR DDRD
#define SPEED1_PIN PIND
#define IS_HIGH_SPEED1 (SPEED1_PIN & (1<<PD2))
#define SET_PULLUP_SPEED1 (SPEED1_PORT |= (1<<PD2))
#define CLEAR_PULLUP_SPEED1 (SPEED1_PORT &= ~(1<<PD2))

// SPEED2 (input)
#define SPEED2 PD3
#define SPEED2_PORT PORTD
#define SPEED2_DDR DDRD
#define SPEED2_PIN PIND
#define IS_HIGH_SPEED2 (SPEED2_PIN & (1<<PD3))
#define SET_PULLUP_SPEED2 (SPEED2_PORT |= (1<<PD3))
#define CLEAR_PULLUP_SPEED2 (SPEED2_PORT &= ~(1<<PD3))

// SW1 (input)
#define SW1 PD6
#define SW1_PORT PORTD
#define SW1_DDR DDRD
#define SW1_PIN PIND
#define IS_HIGH_SW1 (SW1_PIN & (1<<PD6))
#define SET_PULLUP_SW1 (SW1_PORT |= (1<<PD6))
#define CLEAR_PULLUP_SW1 (SW1_PORT &= ~(1<<PD6))

// SW0 (input)
#define SW0 PD7
#define SW0_PORT PORTD
#define SW0_DDR DDRD
#define SW0_PIN PIND
#define IS_HIGH_SW0 (SW0_PIN & (1<<PD7))
#define SET_PULLUP_SW0 (SW0_PORT |= (1<<PD7))
#define CLEAR_PULLUP_SW0 (SW0_PORT &= ~(1<<PD7))


void io_init(){
  PWM0_DDR |= (1<<PB1);
  PWM0_PORT &= ~(1<<PB1);
  PWM1_DDR |= (1<<PB2);
  PWM1_PORT &= ~(1<<PB2);

  OUT0_DDR |= (1<<PB6);
  OUT0_PORT &= ~(1<<PB6);
  OUT2_DDR |= (1<<PB7);
  OUT2_PORT &= ~(1<<PB7);
  ANALOG0_DDR &= ~(1<<PC0);
  ANALOG1_DDR &= ~(1<<PC1);
  LED1_DDR |= (1<<PC2);
  LED1_PORT &= ~(1<<PC2);
  LED0_DDR |= (1<<PC3);
  LED0_PORT &= ~(1<<PC3);
  SPEED1_DDR &= ~(1<<PD2);
  SPEED2_DDR &= ~(1<<PD3);
  SW1_DDR &= ~(1<<PD6);
  SW0_DDR &= ~(1<<PD7);
}


uint16_t ReadChannel(uint8_t mux){
	uint8_t i;
	uint16_t result;

	ADCSRA = (1<<ADEN) | (1<<ADPS2) | (1<<ADPS1) | (1<<ADPS0);    //frequPrescaler 8

	ADMUX = mux; //Kanal
	ADMUX |= (1<<REFS0);  //Vcc RefU
	ADMUX &= ~(1<<REFS1);  //Vcc RefU
	//ADMUX |= (1 << REFS0); //

	ADCSRA |= (1<<ADSC);   // eine ADC-Wandlung Dummy-Readout

	while ( ADCSRA & (1<<ADSC) ) {
		;     //warten bis fertig 
	}
	result = ADCW;
	// echte messung = mittelwert aus 4 messungen
	result = 0; 
	for( i=0; i<4; i++ ){
		ADCSRA |= (1<<ADSC);            // eine Wandlung "single conversion"
		while ( ADCSRA & (1<<ADSC) ) {
			;   // auf Abschluss der Konvertierung warten
		}
		result += ADCW;
		//result += (ADCL | (ADCH << 8));		    // Wandlungsergebnisse aufaddieren
	}
	ADCSRA &= ~(1<<ADEN);             // ADC deaktivieren 
	result /= 4;
	return result;
}

void enable_pwm(void){
  // fast pwm with 10 bit resolution non inverted
  // on OC1A and OC1B
  TCCR1A = (1<<WGM10) | (1<<WGM11) | (1<<COM1A1) | (1<<COM1B1);
#if PWM_CLKDIV == 1024
  TCCR1B = (1<<CS10) | (1<<WGM12);
#elif PWM_CLKDIV == 8192
  TCCR1B = (1<<CS11) | (1<<WGM12);
#elif PWM_CLKDIV == 65536
  TCCR1B = (1<<CS11) | (1<<CS10) | (1<<WGM12);
#elif PWM_CLKDIV == 262144
  TCCR1B = (1<<CS12) | (1<<WGM12);
#else
  #error invalid PWM_CLKDIV value
#endif
}

void disable_pwm(void){
  TCCR1A = 0;
  TCCR1B = 0;
}
void init_pwm(void){
  enable_pwm();
  
  // set default speed to 0
  OCR1A = 0;
  OCR1B = 0;
}
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

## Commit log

2024-08-02 Add firmware 04.2015 - 08.2024
    Firmware used for board V1 developed in 2015 used until 2024
    (from old git repo)
2024-08-02 Add pcb files V1 boards
    Pcbs milled in 05.2015 and V1.1 configuration used until 2024
    [control-2024-07-27-19-54-22.sch, control-2024-07-28-09-19-24.sch, control.kicad_pcb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]
2024-08-02 Add cad files, images, datasheets
    SolidEdge cad files for motor adapter and hinge for rear suspension
    [gelenk.cfg, gelenktest.cfg]
2024-08-02 Add kicad files for board V2 + simulation (WIP)
    Partially copied schematic from previous version but mostly redesigned
    Main changes:
    - Add buck converter for 5V
    - Add low pass filter for 24 supply
    [V2_board-ecar.kicad_pcb, V2_board-ecar.kicad_sch, supply-filter-simulation.kicad_pcb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]
2024-08-04 pcb: Add 2x switch input, split into 3 sheets, remove mosfet output
    [V2_board-ecar.kicad_sch, board-ecar_IO.kicad_sch, input-output.kicad_sch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]
2024-08-04 pcb: change to A3 sheet, re-arrange, minor optimizations
    [V2_board-ecar.kicad_sch]
2024-08-04 pcb: Assign footprints
    [V2_board-ecar.kicad_sch]
2024-08-04 pcb: start layout, arrange components by schematic
    [V2_board-ecar.kicad_pcb, V2_board-ecar.kicad_sch]
2024-08-04 pcb: placed all parts
    [V2_board-ecar.kicad_pcb, V2_board-ecar.kicad_sch]
2024-08-04 pcb: Add moutingholes, fuses
    [V2_board-ecar.kicad_pcb, V2_board-ecar.kicad_sch]
2024-08-04 pcb: layout complete (for review)
    [V2_board-ecar.kicad_pcb, V2_board-ecar.kicad_sch]
2024-08-04 pcb: minor optimizations, swap layers
    [V2_board-ecar.kicad_pcb, V2_board-ecar.kicad_sch]
2024-08-05 pcb: re-arrange schematic, fix track widths
    [V2_board-ecar.kicad_pcb, V2_board-ecar.kicad_sch]
2024-08-06 pcb: Fix footprints, add pcb2gcode conf from ihc-control_pcb project
    [V2_board-ecar.kicad_pcb, V2_board-ecar.kicad_sch]
2024-08-06 pcb: adjust silk, version milled (track missing)
    [V2_board-ecar.kicad_pcb, V2_board-ecar.kicad_sch]
2024-08-07 pcb: Fix missing tracks, Annotate schematic and layout
    [V2_board-ecar.kicad_pcb, V2_board-ecar.kicad_sch]
2024-08-07 pcb: add schem/layout exports, pcb2gcode output
    [V2_board-ecar-B_Cu.gbr, V2_board-ecar-Edge_Cuts.gbr, V2_board-ecar-F_Cu.gbr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]
2024-08-07 Update pin assignments to new board, switch->buzzer, relay, mosfet
    [main.c]
2024-08-07 Remove Uart+Pins, Rename pins - PWM, I/O Pins test success
    Successfully tested the new board
    (switches control outputs, PWM Gate output works with poti input)
2024-08-07 Patch main.c with uncommitted old code (full on, fan...)
    Add all features of current firmware according to
    old firmware (which was previously not available)
2024-08-08 Add 3x beep at startup
    Note: wired pcb and tested with current (reused old) firmware.
    Currently having same issues as in V1.0 with controller crashing at
    motor run, but not when supplied with separate power supply
    [main.c]
2024-08-09 Add uncommitted firmware changes of old project (full on, fan)
    Final version of old firmware used for several years
2024-08-09 Add missing pcb files for old separate driver board (V1.1)
    Add uncomitted files from old repository
    [treiber-2024-08-09-21-46-33.sch, treiber.kicad_pcb, treiber.kicad_sch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]
2024-08-10 Add exports of old versions, Rename 2.0, List pcbs in README
    [V2_board-ecar.kicad_pcb, V2_board-ecar.kicad_sch, board-ecar_IO.kicad_sch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]
2024-08-11 Add wiring-plan
2024-08-19 pcb: Start control-board V2.1 (copy V2.0)
    [V2.1_board-ecar_isolated.kicad_pcb, V2.1_board-ecar_isolated.kicad_sch, board-ecar_IO.kicad_sch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]
2024-08-20 pcb: Schematic: Isolated supply, Optocouplers...
    [V2.1_board-ecar_isolated.kicad_sch]
2024-08-22 pcb: small additions, begin footprint placment
    [V2.1_board-ecar_isolated.kicad_pcb, V2.1_board-ecar_isolated.kicad_sch]
2024-08-23 pcb: optimize placement, assignment
    [V2.1_board-ecar_isolated.kicad_pcb, V2.1_board-ecar_isolated.kicad_sch]
2024-08-24 pcb: routing, pre gnd-plane
    [V2.1_board-ecar_isolated.kicad_pcb, V2.1_board-ecar_isolated.kicad_sch]
2024-08-24 pcb: gnd-planes, testpoints, optimize, pcb2gcode - milling
    [V2.1_board-ecar_isolated.kicad_pcb, V2.1_board-ecar_isolated.kicad_sch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]
2024-08-24 pcb: optimize silk, change values
    [V2.1_board-ecar_isolated.kicad_pcb, V2.1_board-ecar_isolated.kicad_sch]
2024-08-25 Adjust pin assignment, test IO
2024-08-25 V2.1 pcb finished, exports, photos, readme
    [V2.1_board-ecar_isolated.kicad_pcb, V2.1_board-ecar_isolated.kicad_sch]
2024-08-26 pcb: Assign models, Add 3d-model export
    [V2.1_board-ecar_isolated.kicad_pcb, V2.1_board-ecar_isolated.kicad_sch]
2024-08-26 Start Rewrite of firmware - gpio, adc, pwm
    Used some code of recent project throttle-adjust (electric-lawnmower) - mostly uart, adc
    But mostly created code from scratch e.g. gpio library
2024-08-27 PWM-Freq tests log, logging, basic IO-test - success
    Board installed and successfully tested
    All practical pwm frequencies were tested
    Basic IO pass through (buzzer at low voltage, fan at switch...)
    [main.c]
2024-08-28 Add cycle through preset configs (pwm) with button
2024-08-28 Fix pwm-init, Fix Fan, Add slow-mode, lowBatt beep at pedal release, LED-on, more Fan
    - long button press toggles slow mode on/off
    [main.c]
2024-08-28 Update wiring-plan, readme, Add cad-file box
    [box-control.FCStd]
2024-08-29 Add Timer2 ISR to track time precisely in ms
    Replace the hacky unreliable method counting up in main loop
    [main.c]
2024-08-29 Add buzzer.h - non-blocking beeping, remove delays
    [main.c]
2024-08-30 Outsource pwm code, Add +2 config presets, Fix led
    [main.c]
2024-08-30 Add Switch to default config at maxTimeOnContinuous config option
2024-09-11 pcb: Update schematic (mosfet name, actual R value)
    [V2.1_board-ecar_isolated.kicad_sch]
